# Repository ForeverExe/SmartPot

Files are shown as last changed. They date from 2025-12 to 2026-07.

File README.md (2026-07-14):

# Smart Pot
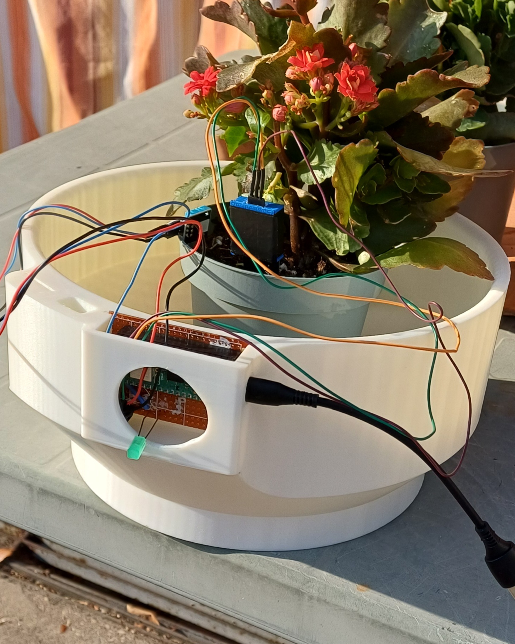
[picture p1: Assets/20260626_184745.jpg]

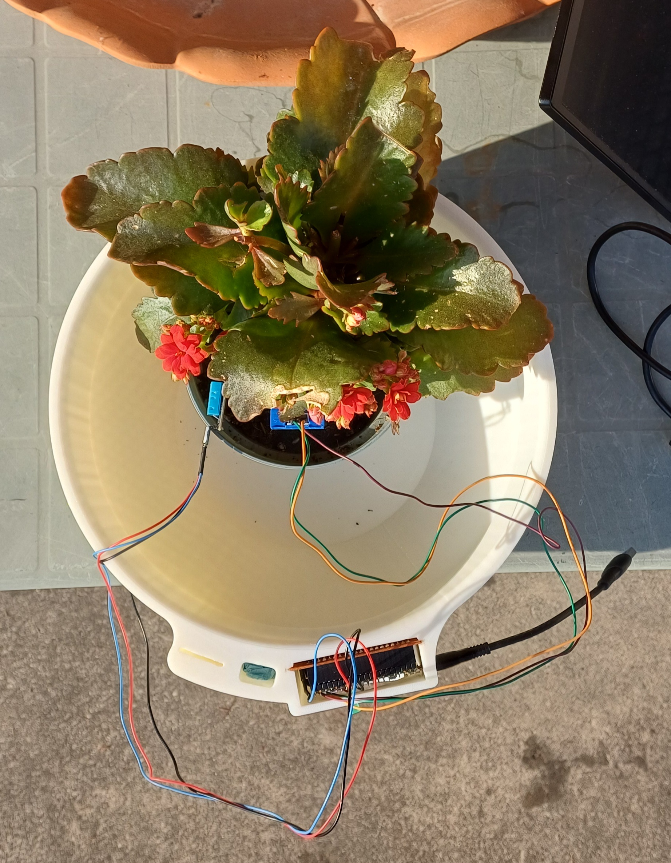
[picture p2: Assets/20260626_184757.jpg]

<br>

# Summary
<!-- TOC -->
* [Bill of Materials](#bill-of-materials)
* [Structure](#structure)
    * [The CircuitPython device](#the-circuitpython-device)
    * [The Java Application](#the-java-application)
        * [Java structure](#java-structure)
* [The MQTT Structure](#the-mqtt-structure)
* [Known Issues](#known-issues)
* [Gallery](#gallery)
<!-- TOC -->

The Smart Pot is a project done for @piconem 's Intelligent Internet of Things class at Universitá di Modena e
Reggio Emilia (UniMoRe) - Sede di Mantova.  
The device is a support for any plant that wants to be monitored, you just need to place the vase (or dirt directly)
inside it and to position both the sensors and actuators.

At its actual state, it can track and send via MQTT the plant's telemetry, its information for discovery and update its
settings by using a dedicated topic which it's subscribed to.

On the other side, a desktop Java application runs as a hub to list which devices have been discovered, read their telemetry
and update their settings.

# Bill of Materials

- 1x Raspberry Pi Pico 2W (or any other kind of pico, as long it can be connected to a network)
- 1x Capacitive Soil Humidity Sensor (v1.2 in this case)
- 1x DHT11 Air Humidity and Temperature sensor
- Cables as needed
- 1x Perfboard (around 5x7cm)
- 1x Green LED (substitutes)
- 1x 1k Ohm Resistor
- 1x Printed SmartPot (Tolerances not accounted for)

The print can be done in any printer with a bed greater or equal 256^3 cm, just make sure you print it with some wear/weather resistant material like PETG or ASA/ABS.  
The model has been made using FreeCAD and then sliced in OrcaSlicer.

---

# Structure

The project is basically divided in two parts:

- The CircuitPython application which runs on the Raspberry pico
- The Java desktop app

### The CircuitPython device

The SmartPot device is running with one of the latest CircuitPython releases, which has been loaded and programmed with
"Thonny". This way, it can also support the Raspberry Pi Pico W (the non W-versions need an external adapter,
which the code does not contemplate).
The main libraries that are being used for this project are all coming from adafruit's official and community packages,
especially:

- miniMQTT
- DHT
- SenML
- analogio

The CircuitPython logic runs on three files:

- **code.py**: Main logic file, manages the MQTT connection and both transmission and receive of data. Data like credentials, etc, are taken from the `settings.yaml` file contained inside the CircuitPython environment.
- **Sensors.py**: A class which contains all the logic regarding both sensors and actuators initialization while also giving helper functions to read from the sensors.
- **Settings.py**: A class which represents the device's triggers and timers. Has getter and setters for each one of them to be used when receiving new settings from the Java app or when publishing them to the broker.

If debugging or more details are needed, the device prints in Thonny's stdout.

The Device reads and prepares a Json+SenMLPack containing every telemetry available and publishes it to the `t` topic.
It also prepares and publishes via Json+SenMLRecord the single telemetry values so they could be obtained singularily (not used in the app for simplicity.)

##### Code Flow:
- Initializes the various sensors and settings object and tries to connect to an available 2.4GHz WiFi connection.
- Publishes its information at the `ì` topic with the CPU's UID as its "root topic".
- Starts reading and publishing the telemetry every loop
- Updates its settings if new ones are uploaded in the broker.

---

### The Java Application

The Java application, other than the standard library, only uses Google's `Gson` and Eclipse's `Paho MQTT`.
It can read and create SenML records and packs, but it uses a makeshift version. Since it follows the standard, it can communicate seamlessly with Adafruit's SenML.

A TUI menu enables the user to easily navigate the options given:

- Read the list of connected device
- Read and change the settings of the selected device
- Read the selected device's telemetry

At startup, it subscribes to the device's Settings, Info and Telemetry topics to start adding the device to the internal list and synchronize their information and settings. After that it will start updating their telemetry values and unsubscribe to the Settings topic in order to publish on it later.

##### Java structure

- **SmartPotDescriptor**: Object which represents a single SmartPot, containing general information like model, version, name and the
device's uuid. Also contains the settings and telemetry objects, so everything is being accessed through this.
- **SmartPotSettings**: A Basic POJO containing all the settings used by the device. It gets synchronized at startup via subscribe and then unsubscribes after finishing syncing.
- **SmartPotTelemetry**: POJO used to store the device's telemetry, it gets updated frequently, based on the device's "refreshTimer" option.

- **SmartPotServer**: The name of the app which uses the aformentioned objects, it connects to the broker, creates the devices' list, prepares and responds to user interaction thanks to the TUI.

- **DeviceSim** is a partial device simulator that only sends information data, *not intended for actual use*.

##### Code Flow
- At startup, Discovery is performed and adds to its memory each device it can find by using their `#/i` topic.
- It gets their telemetry and their settings from the broker to update itself.
- Now it waits for a user command, meanwhile it still gets their telemetry updated asynchronously.
---

# The MQTT Structure

MQTT is the communication method chosen for the project. It uses the professor's Mosquitto instance as a broker and it's divided by
the device's UUID, which is not available per-se in circuitpython, so it uses the ID of the device's CPU.

```
root  
├── uuid1  
│   ├── i (Device Information)
│   ├── s (Device Settings)  
│   └── t (Device Telemetry)  
│       ├── ah (Air Humidity)  
│       ├── sh (Soil Humidity)  
│       └── tmp (Air Temperature)  
├── uuid2  
├── ...  
└── uuidN  
```

| Topic | Pub | Sub | QOS | Retained |
| ----| ----  | --- | --- |  --- |
|uuid | Pico  | App | 1 |  true  |
| i | Pico  | App | 1 |  true  |
| s | App | Pico| 1 |  true  |
| t | Pico  | App |  0  |  false |
| ah  | Pico  | App |  0  |  false |
| sh  | Pico  | App | 0 |  false |
| tmp | Pico  | App | 0 |  false |

(For simplicity, "ah", "sh" and "tmp" are not implemented in the app logic)

# Known Issues

- Messages used for discovery (device info) and settings should be sent with a QOS 2 for major certainty of correct message delivery, but *QOS 2 is not yet implemented in adafruit's publish method*.
- The printed model has some tolerance issues in the area dedicated to slot the electronics. The areas are needed to be increased in size or lightly milled in order to fit.

# Gallery

Demo Video (https://youtu.be/0ZKRhLkEHeQ)

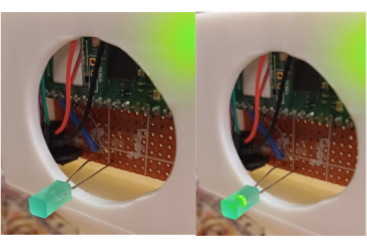
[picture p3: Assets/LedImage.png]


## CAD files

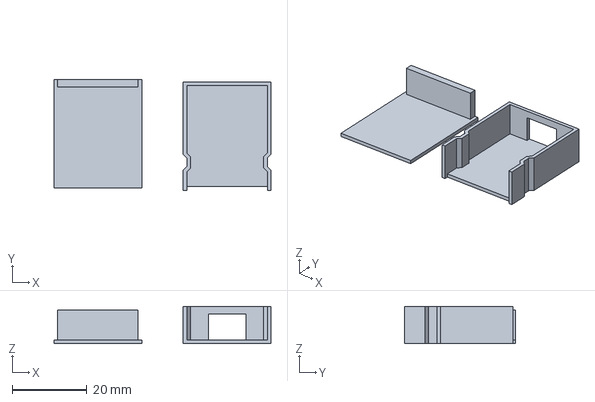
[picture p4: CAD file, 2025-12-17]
CADModels/3DPrinting/CoperturaSensHum-Copertura alta.3mf
58.1 x 29.6 x 10.0 mm

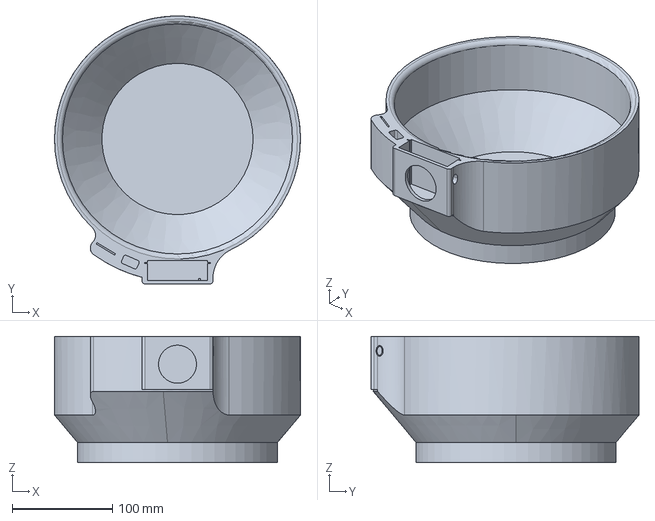
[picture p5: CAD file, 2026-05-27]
CADModels/ProtoPot.FCStd
246.0 x 268.0 x 126.0 mm

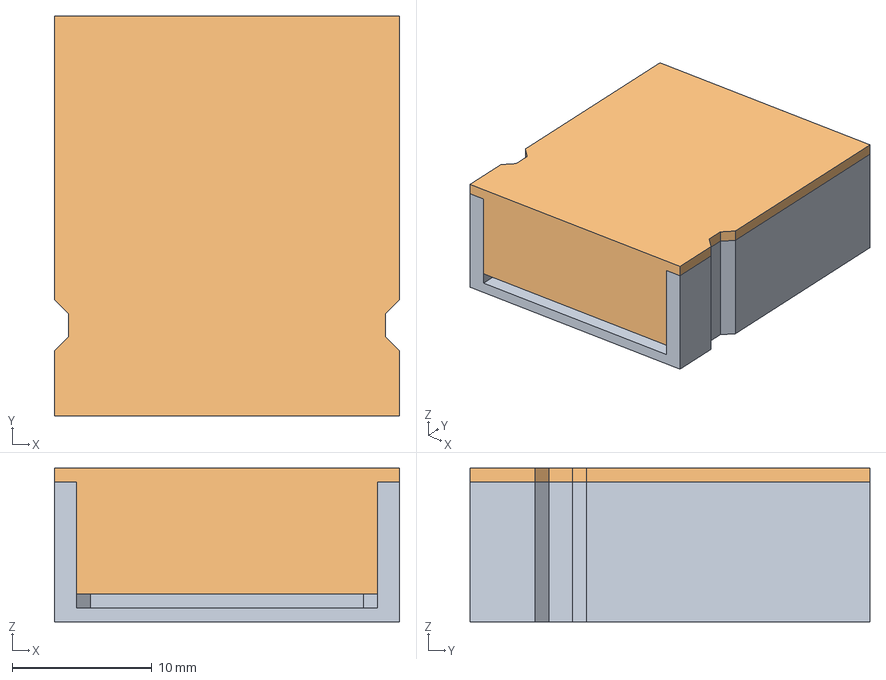
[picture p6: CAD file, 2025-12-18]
CADModels/CoperturaSensHum.FCStd
24.7 x 28.6 x 11.0 mm
Copertura Principale
Copertura alta

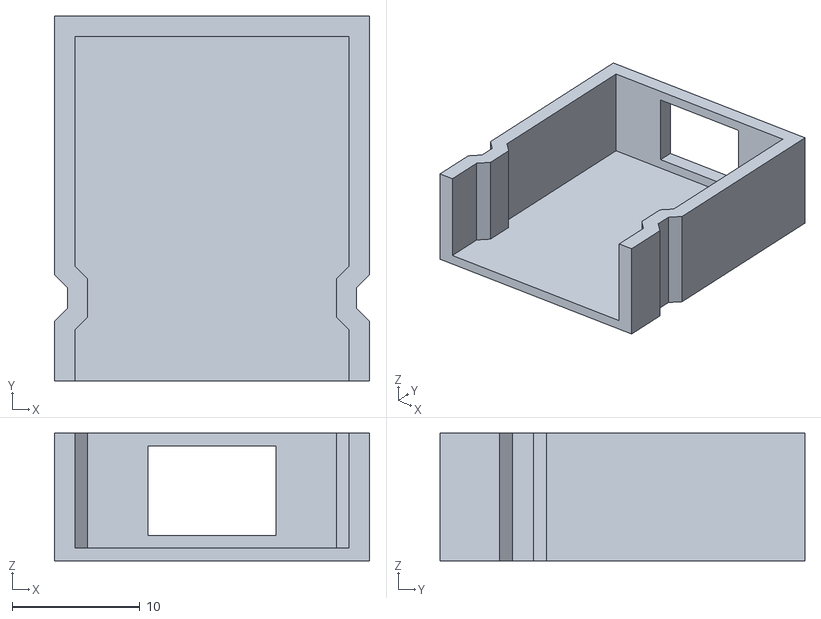
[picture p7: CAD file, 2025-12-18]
CADModels/CoperturaSensHum-Copertura Principale.stl
24.7 x 28.6 x 10.0

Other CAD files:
CADModels/3DPrinting/ProtoPot.stl
CADModels/CoperturaSensHum-Copertura alta.stl

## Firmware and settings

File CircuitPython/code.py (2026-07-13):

from os import getenv

import adafruit_logging
import time
import board
import adafruit_connection_manager
import wifi
import microcontroller
import json
import adafruit_minimqtt.adafruit_minimqtt as MQTT

from PotSettings import PotSettings
from senml import *
from Sensors import Sensors

############## VARIABLES AND ALMOST-CONSTANTS #############

mqtt_username = getenv("MQTT_USERNAME")
mqtt_password = getenv("MQTT_PASSWORD")
mqtt_ip = getenv("MQTT_IP")
mqtt_port = int(getenv("MQTT_PORT"))

uuid = microcontroller.cpu.uid.hex()
print(f"UUID using the processor hex'd UID: {uuid}")

basic_topic = getenv("MQTT_BASIC_TOPIC")+'/'+uuid #--> /device/<uuid>
print(f"Basic topic of the device: {basic_topic}")

subscribe_feed = basic_topic+getenv("MQTT_DEVICE_SETTINGS_TOPIC") #--> /device/<uuid>/settings
tel_topic = basic_topic+getenv("MQTT_BASE_TELEMETRY") #--> /device/<uuid>/telemetry
info_topic = basic_topic+getenv("MQTT_DEVICE_INFO_TOPIC") #--> /device/<uuid>/info
will_topic = basic_topic+getenv("MQTT_WILL_TOPIC")
print("Main Topics:")
print(f"Settings: {subscribe_feed}\nTelemetry: {tel_topic}\nInformation: {info_topic}\n")

sh_topic = tel_topic+getenv("MQTT_TEL_SH")
ah_topic = tel_topic+getenv("MQTT_TEL_AH")
temp_topic = tel_topic+getenv("MQTT_TEL_TEMP")
print("Telemetry Topics:")
print(f"- {sh_topic}\n- {ah_topic}\n- {temp_topic}\n")

device_info ={'name':'SmartPot Proto1','uuid':uuid,'version':'0.0.2','type':'Raspberry Pi Pico2W'}
json_info = json.dumps(device_info, separators=(',',":"))
print(f"Info:\n{device_info}")
settings = PotSettings()
print(f"Settings:\n{settings}")

DHT_PIN = board.GP14
LED_PIN = board.GP13
SOIL_PIN = board.GP28_A2
#LED_PIN = board.GP5

############# LOGIC #############

sens= Sensors(DHT_PIN, SOIL_PIN, LED_PIN)

### MQTT Client methods
def connected(client, userdata, flags, rc):
    print("Done! Publishing the device informations...")
    print(str(rc)+"\n\n")
    mqtt_client.publish(info_topic, json_info, True, 1)

def disconnected(client, userdata, rc):
    print("Disconnected from the Broker")
    
def message(client, topic, message):
    print(f"New message on topic {topic}: {json.loads(message)}")

def apply_settings_msg(client, topic, message):
    print("Settings received, applying settings")
    print(f"Old Settings:\n{settings}")
    msg = json.loads(message)
    print(str(msg))
    settings.set_refresh(msg['refreshTimer'])
    settings.set_air_hum_trigger(msg['ahTrigger'])
    settings.set_soil_hum_trigger(msg['shTrigger'])
    settings.set_temp_trigger(msg['tempTrigger'])
    settings.set_water_timer(msg['waterTimer'])
    print(f"New Settings:\n{settings}")
    
#### Pot Methods
def update_and_send():
    try:
        print("TempRecord")
        #1 pack, 4 record, tutte da pubblicare
        tpack = SenmlPack("")
        #ah = SenmlRecord("air_hum", unit=SenmlUnits.SENML_UNIT_RELATIVE_HUMIDITY, value=random.uniform(10.0,40.0), time=time.time())
        #sh = SenmlRecord("soil_hum", unit=SenmlUnits.SENML_UNIT_RELATIVE_HUMIDITY, value=random.uniform(20.0,50.0),time=time.time())
        #temp = SenmlRecord("temperature", unit=SenmlUnits.SENML_UNIT_DEGREES_CELSIUS, value=random.randint(0,40), time=time.time())
        ah = SenmlRecord(name="air_hum", unit=SenmlUnits.SENML_UNIT_RELATIVE_HUMIDITY, value=float(sens.get_air_hum()), time=time.time())
        sh = SenmlRecord(name="soil_hum", unit=SenmlUnits.SENML_UNIT_RELATIVE_HUMIDITY, value=float(sens.get_soil_hum()),time=time.time())
        temp = SenmlRecord(name="temperature", unit=SenmlUnits.SENML_UNIT_DEGREES_CELSIUS, value=int(sens.get_temp()), time=time.time())
        tpack.add(ah)
        tpack.add(sh)
        tpack.add(temp)
        jsonOut = tpack.to_json()
        
        jstruct = json.loads(jsonOut)
        print(jstruct[0])
        print(jstruct[1])
        print(jstruct[2])
        
        mqtt_client.publish(tel_topic, jsonOut, True, 0)
        mqtt_client.publish(ah_topic, json.dumps(jstruct[0]), False, 0)
        mqtt_client.publish(sh_topic, json.dumps(jstruct[1]), False, 0)
        mqtt_client.publish(temp_topic, json.dumps(jstruct[2]), False, 0)
    except (ValueError, RuntimeError) as e:
        print("Error publishing the data...\n", e)
        
    
#### MAIN
try:
    # Connect to the Wi-Fi network
    wifi.radio.connect(ssid = getenv("TEL_SSID"), password = getenv("TEL_PASSWD"))
except OSError as e:
    print(f"Mobile Network not found, switching to secondary network")
    wifi.radio.connect(ssid = getenv("WIFI_SSID"), password = getenv("WIFI_PASSWORD"))

print("Connected to Wifi!")
print("My IP addr:", wifi.radio.ipv4_address)

pool = adafruit_connection_manager.get_radio_socketpool(wifi.radio)
ssl_context = adafruit_connection_manager.get_radio_ssl_context(wifi.radio)

mqtt_client = MQTT.MQTT(
    broker = mqtt_ip,
    port = mqtt_port,
    username = mqtt_username,
    password = mqtt_password,
    client_id = "Pot"+uuid,
    socket_pool = pool,
    ssl_context = ssl_context,
    use_binary_mode = True,
)

logger = mqtt_client.enable_logger(adafruit_logging, adafruit_logging.INFO, "loggy")

mqtt_client.on_connect = connected
mqtt_client.on_disconnect = disconnected
mqtt_client.add_topic_callback(subscribe_feed, apply_settings_msg)

mqtt_client.will_set(will_topic, "Device Disconnected", False, 1)

try:
    print("Connecting to the broker...")
    mqtt_client.connect()
    print("Connection Established: subscribing and listening to the settings topic...")
    mqtt_client.subscribe(subscribe_feed, 1)
except (ValueError, RuntimeError) as e:
    print("Failed to connect, retrying")
    wifi.reset()
    mqtt_client.reconnect()
    

while True:
    try:
        update_and_send()
        mqtt_client.loop(float(settings.get_refresh()))
        if(sens.get_soil_hum() < settings.get_soil_hum_trigger()):
            sens.activate_led()
            time.sleep(settings.get_water_timer())
            sens.deactivate_led()
            
    except (ValueError, RuntimeError) as e:
        print("Failed to get data, retrying\n", e)
        wifi.reset()
        mqtt_client.reconnect()
        continue
    time.sleep(1)

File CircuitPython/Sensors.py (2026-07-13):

import board
import time
import adafruit_dht
from analogio import AnalogIn
from digitalio import DigitalInOut, Direction, Pull

class Sensors(object):

    def __init__(self, dht_pin, soil_pin, led_pin):
        self.DRY_VALUE = 65535
        self.WET_VALUE = 40000
        self.dht = adafruit_dht.DHT11(dht_pin)
        self.soil_device = AnalogIn(soil_pin)
        self.led = DigitalInOut(led_pin)
        self.led.direction = Direction.OUTPUT
        self.led.value = False

    def hum_percent(self, pin, campioni):
        somma = 0
        for _ in range(campioni):
            somma = somma + pin.value
            time.sleep(0.005)  # Breve pausa tra i campioni
        
        somma= somma//campioni
        
        #print(f"Debug: Voltaggio {(somma*3.33)/65535}")
        
        perc = ((self.DRY_VALUE - somma) / (self.DRY_VALUE - self.WET_VALUE)) * 100
        if perc < 0:
            return 0
        elif perc > 100:
            return 100
        
        return round(perc,1)

    def get_air_hum(self):
        return self.dht.humidity

    def get_temp(self):
        return self.dht.temperature

    def get_soil_hum(self):
        return self.hum_percent(self.soil_device, 20)

    def activate_led(self):
        self.led.value = True
        return self.led.value
    
    def deactivate_led(self):
        self.led.value = False
        return self.led.value

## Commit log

2025-12-16 init repo
    [CoperturaSensHum.FCStd]
2025-12-16 caricamento sottovaso
    [PotBase.FCStd]
2025-12-17 upload modelli e stampa3d
    [CoperturaSensHum-Copertura Principale.stl, CoperturaSensHum-Copertura alta.3mf, CoperturaSensHum-Copertura alta.stl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]
2025-12-17 avanzamento modello e test funzionante mqtt pico2
    [PotBase.FCStd]
2025-12-18 allargato un po il modello del sensore
    [CoperturaSensHum-Copertura Principale.stl, CoperturaSensHum-Copertura alta.stl, CoperturaSensHum.FCStd]
2025-12-20 modelli aggiornati e codice python
    [PotBase.FCStd]
2025-12-22 Update al codice java ed un po' di python
2026-01-15 FIXATO, NON USARE QOS2 IN PUBLISH
    [code.py]
2026-02-04 Principio di main menu
2026-02-16 minor fixes
    [SmartPotCircuit.kicad_pcb, SmartPotCircuit.kicad_sch]
2026-02-22 MQTT Finito al 99%, manca l'hardware esterno e la parte "server"
2026-03-05 vedere perche' non va il sub
2026-04-14 FEAT: Riempimento Lista Device ed aggiornamento settings funzionante. Rimane lettura telemetria. Rimane lettura sensori. Rimane output a tft
2026-05-15 nuovo modello da bucare
    [Base2.FCStd, PotBase.FCStd]
2026-05-21 update modello, misurare sensori da mettere
2026-05-21 aggiunto file di prova per i sensori
2026-05-22 lettura fattibile, servono 5v
2026-05-22 inizio behaviour sensori
2026-05-22 inizio sviluppo sensori
2026-05-26 Test di Stampa
    [Base2.FCStd, Potcore.FCStd, VasoTest.stl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]
2026-05-27 modifica pot
    [Base2.FCStd, ProtoPot.stl, VasoTest2.stl]
2026-06-12 da implementare la logica su core, poi rifare circuito
2026-06-22 applicazione sensori su programma principale
2026-06-24 Readme quasi finito, giusto un controllo. Ora gli oggetti device sincronizzano i settings all'avvio.
2026-06-24 sprint finale
    [PotBase.FCStd, Potcore.FCStd, ProtoPot.FCStd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]
